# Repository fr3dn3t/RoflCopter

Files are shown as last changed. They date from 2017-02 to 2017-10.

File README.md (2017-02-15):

# RoflCopter
My RoflCopter makes swush swush swush - just kidding. The RoflCopter a monocopter, monospinner, gyropter, drone whatever you want to call it. 

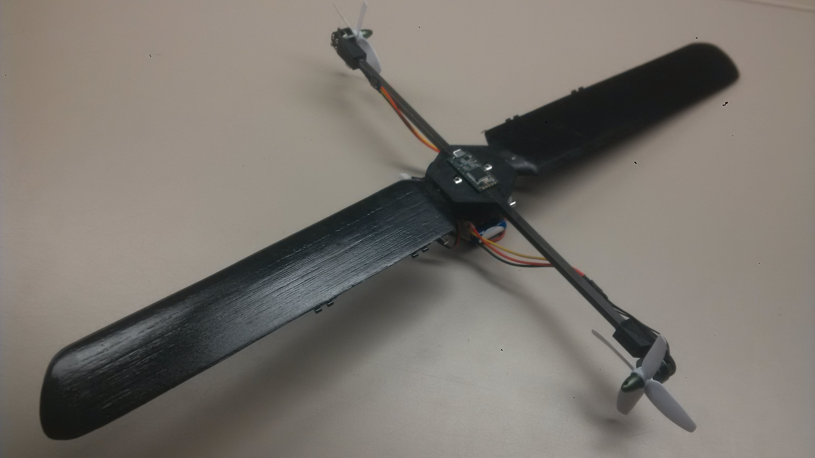
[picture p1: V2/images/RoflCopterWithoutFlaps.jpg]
roflCopter


I'm working on this project since October 2015 and until now, there have been two versions. The first Version was built to test various parameters and hardware approaches to make it fly - Version 1 was completed in May 2016, but never flew.
Applying the lessons learned from the first version I started to build a secont one. This one was completly designed via CAD and the rotor blades were simulated in XFLR5. A full documentation can be found in V2/docs/ (german only), the first successful flight was on 14th February 2017 [Video](https://github.com/fr3dn3t/RoflCopter/blob/master/V2/videos/RoflCopter%20-%20FirstFlight14022017.mp4)

more to come

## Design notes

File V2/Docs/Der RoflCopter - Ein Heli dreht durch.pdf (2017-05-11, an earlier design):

# Der roflCopter - Ein Heli dreht durch

### Jugendforscht Technik 2017

### Frederik Dunschen

### 24. Februar 2017

Zusammenfassung

Was bedeutet es, ein eigenes Konzept fur ein Flugger ¨ | ät zu entwerfen, zu konstruieren und
letztendlich die Algorithmen fur die Flugsteuerung zu implementieren? Dies untersuche ¨ ich in diesem Projekt anhand des RoflCopters. Der RoflCopter ist ein von mir entworfenes Kleinstfluggerät, das auf dem Prinzip eines Monocopters basiert. Das bedeutet, dass der
Auftrieb uber zwei Rotorbl ¨ | ätter erfolgt, die am Gehäuse des Copters befestigt sind. Das
gesamte System wird von zwei Motoren an einem Motorausleger in Rotation versetzt
und der Auftrieb uber den Anstellwinkel der Rotorbl ¨ | ätter gesteuert. Um seine Lage bzw.
Position im Raum zu ändern, besitzt der RoflCopter zwei Steuerklappen an den beiden Rotorblattspitzen. Doch dieser Aufbau allein reicht nicht aus, um ein flugfähiges Gerät zu erhalten. Dazu ist auch ein Algorithmus nötig, der Steuerbefehle einließt, die nötigen Steueraktionen berechnet und schließlich, abgestimmt auf die Hardware, ausfuhrt. ¨

# Inhaltsverzeichnis

1 Einleitung | 3
2 Projektablauf | 5
3 Aufbau und Funktion | 6
4 Algorithmik | 11
5 Fazit | 16
6 Verzeichnisse | 17

# Kapitel 1

# Einleitung

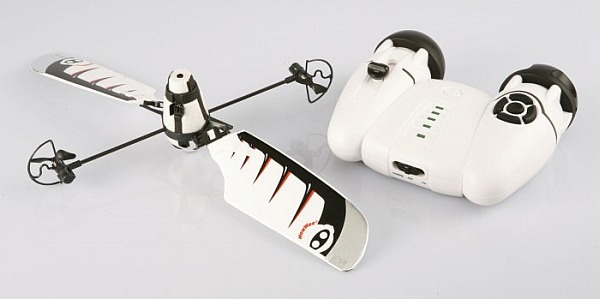
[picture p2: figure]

Abbildung 1.1: Bladestar [1]

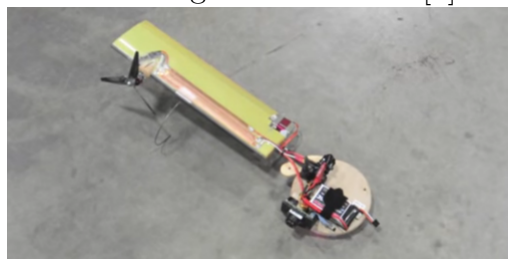
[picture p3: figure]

Abbildung 1.2: Samari UAV [2]

Der Traum vom Fliegen beflugelt seit jeher die ¨
kuhnsten Tr ¨ | äume der Menschheit. Waghalsige Kon-
struktionen folgten auf halsbrecherische Ideen und unzählige Absturze auf zahllose Flugversuche. Die ¨ ersten funktionierenden Fluggeräte, Flugzeuge wie Helikopter, ließen sich ausschließlich uber Mechani- ¨ ken steuern und fliegen, der Pilot bewegte Klappen und Ruder allein durch Muskelkraft. Undenkbar fur ¨ heutige Fluggeräte - Autopiloten und Flugassistenzsysteme nehmen Piloten viel Arbeit ab, Sensoren uberwachen jede kleinste Bewegung und Motoren ¨ fahren Klappen und Ruder aus und ein. Microcontroller und Computer haben jedoch nicht nur in großen Verkehrsmaschinen und Helikoptern Einzug gehalten. Sie ermöglichten Kleinstfluggeräte mit Konzepten, die mit einfacher Mechanik nicht realisierbar wären. Multicopter dienen hierfur als ¨
besonderes Beispiel: Die kleinen Fluggeräte sind
simpel Aufgebaut, flögen von sich aus jedoch nicht
stabil in der Luft. Erst die Flug- und Lageregelung durch einen kleinen Computer, einen
Microcontroller, erlaubt auch ungeubten Piloten das einfache Fliegen dieser Ger ¨ | äte. Der
Pilot steuert nicht mehr direkt, er gibt lediglich seinen Steuerwunsch an den Microcontroller weiter. Dieser kann die Daten, die fur die Steuerung relevant sind, wesentlich schneller ¨ und genauer messen, auswerten und interpretieren, um so das Fluggerät in Zusammenspiel mit der Mechanik letztendlich zu steuern.
Uber die letzten Jahre sind die Leistungsdaten von Microcontrollern erheblich gestiegen ¨
und die Preise gefallen. Das lässt nicht nur die Anzahl der verfugbaren, g ¨ | unstigen Kleinst- ¨
fluggeräte steigen, sondern ermöglicht es auch, innerhalb eines uberschaubaren Preisrah- ¨
mens, selbst ein Konzept fur ein Kleinstflugger ¨ | ät zu entwickeln und umzusetzen. Genau
dies habe ich mit dem roflCopter getan.
Der roflCopter ist zuerst einmal ein Rotationsflugler (daher der Name), er erzeugt den ¨ benötigten Auftrieb also durch einen rotierenden Flugel bzw. Rotor. Des weiteren ist er ¨ ein Fluggerät, dass von seiner Bauform her eine Art Monocopter ist. Ein Monocopter zeichnet sich dadurch aus, dass er nur ein Rotorblatt und keinen Drehmomentausgleich, wie beispielsweise den Heckrotor eines Helikopters hat. Das bedeutet, dass sich nicht nur der Rotor, sondern das gesamte Fluggerät in der Luft dreht. So ist es naturlich schwierig, ¨

KAPITEL 1. EINLEITUNG

in der Luft sowohl eine ruhige Fluglage, als auch eine Steuerung uber alle Achsen zu er- ¨ halten.
Der roflCopter basiert im Prinzip auf den Konzepten des “WowWee Bladestar” (Abb.: 1.1) und des “Lockheed Martin Samari UAV” (Abb.: 1.2). Diese Konzepte habe ich zusam-
mengefuhrt, da sie sich gegenseitig in ihren Vor- und Nachteilen erg ¨ | änzen. Der “WowWee
Bladestar” soll sich zwar steuern lassen, der technische Aufbau des Produktes lässt dies allerdings nicht zu: die Rotorblätter sind auf einen Winkel fest angestellt und nur die Motoren lassen sich in ihrer Umdrehungsgeschwindigkeit steuern. So lässt sich die Lage des
Copters naturlich nicht ver ¨ | ändern, das Fluggerät kann seine Position im Raum lediglich
auf der Z-Achse verändern, also steigen oder sinken.
Der “Lockheed Martin Samari UAV” hat, anders als der Bladestar, eine aktive Lageregelung. Hier ist auch der technische Aufbau ein anderer, es handelt sich um einen klassischen Monocopter bzw. Gyropter - die Entwickler haben sich von einem Ahornsamen inspirieren lassen. Doch durch den asymetrischen Aufbau und die daraus entstandene Unwucht fliegt der Copter nicht ruhig.
Ich versuche nun die Vorteile beider Konzepte zu verbinden: Den symetrischen Aufbau des “WowWee Bladestar” und die aktive Steuerung des “Lockheed Martin Samari UAV”. Mit diesem Projekt möchte ich untersuchen, wie aufwändig es ist und was es bedeutet, ein selbst konzipiertes Kleinstfluggerät zu entwickeln, das nur uber eine eigene, neuartige ¨ Flugsteuerung gesteuert werden kann. An Monocoptern als elektrisch betriebene Kleinstfluggeräte wird vergleichsweise wenig geforscht, es gibt nur vereinzelte Forschungsarbeiten von Universitäten wie der ETH Zurich [3], dem MIT [4], sowie der University of Maryland ¨
[5] und Firmen wie Lockheed Martin [6]. Auch dieser Umstand hat mich besonders an dem Bau eines solchen Fluggerätes gereizt, da ich nahezu alles selbst entwickeln muss. Eine weitere Herausforderung ist naturlich, die Hardware und die Software so zu konzipieren ¨ und aufeinander abzustimmen, dass sie möglichst schnell und präzise Steuerbefehle und Sensoren einlesen, die nötigen Berechnungen vornehmen und die jeweiligen Steueraktionen in entsprechende Flugbewegungen uberf ¨ uhren kann. ¨

# Kapitel 2

# Projektablauf

Die Idee fur den roflCopter hatte ich bereits im September 2015. Ich habe die ersten ¨
Entwurfe gemacht und angefangen, Bauteile f ¨ | ur einen Prototypen zu fertigen und zu be- ¨
stellen.
Den ersten Satz Rotorblätter habe ich im Oktober 2015 gefertigt. Diese habe ich an ein Grundgerust, bestehend aus dem Motorausleger mit entsprechenden Motoren, Motorreg- ¨ lern und Servos, angebracht. Gegen Ende Oktober habe ich mit der Steuerelektronik und der Software angefangen. Zu diesem Zeitpunkt hatte ich noch keine Steuerklappen vorgesehen, sondern wollte die Servos an den Rotorblättern zur Steuerung benutzen. Es hat sich jedoch herausgestellt, dass diese in ihrer Reaktion zu träge sind. Deshalb habe ich nach einer anderen Lösung gesucht und bin so auf die linearen Magnetaktuatoren gekommen. Im November und Dezember 2015 habe ich mich mit der Lagesensorik beschäftigt. Ich habe zunächst auch einen Kompasssensor verbaut, musste jedoch feststellen, dass dieser
Sensor zu langsam fur eine genaue Messung w ¨ | ährend der Rotation war.
Im Januar 2016 habe ich die Steuerklappen an den Rotorblättern installiert und die Elektronik zur Ansteuerung der Magneten entworfen. Sowohl die Schaltung, als auch die Klappenmechanik hat sich bewährt und ist bis heute die selbe geblieben. Im März habe ich die grundlegenden mathematischen Algorithmen zu Stabilisierung und Lageänderung entworfen und mit dem Bau des Infrarotmoduls begonnen.
Im April konnte ich anfangen, alle einzelnen Module fur die erste Version des Copters ¨ zu testen und zu verbessern. Ende April habe ich mit den Tests des gesamten Systems angefangen und konnte dabei Umdrehungsgeschwindigkeiten und Lagemessungen prufen. ¨ Die erste Version des roflCopters war fertig und ich konnte im Mai meine Facharbeit uber den Copter abgeben. Letztendlich hat sich jedoch herausgestellt, dass erste Ver- ¨
sion zwar genugend Auftrieb f ¨ | ur einen Flug erzeugt, jedoch trotzdem flugunf ¨ | ähig ist:
Die Aufhängung der Rotorblätter war zu instabil, die elektronischen Komponenten nicht geordnet bzw. symmetrisch aufgebaut und der gesamte technische Aufbau nicht aerodynamisch durchdacht.
Ab September habe ich eine zweite Version des Copters auf der Grundlage der Erkenntnisse der ersten Version konzipiert. Diesmal begann ich nicht mit dem Bau, sondern fing an, das System als 3D Modell zu entwerfen und wichtige Teile, wie die Rotorblätter, am
Computer zu simulieren. Daruber hinaus habe ich gepr ¨ | uft, welche Komponenten in der ¨
ersten Version wie gewunscht funktionierten und welche ich ersetzen musste. Die wich- ¨ tigste Anderung war die Konzeption eines um einen Lagerblock zentralisierten Aufbaus. ¨ Die Elektronik ist in der zweiten Version auch nicht mehr lose verkabelt, sondern auf einer Platine unter dem Lagerblock angebracht. Mit dem Bau der zweiten Version beschäftige ich mich seit Oktober 2016, der erste erfolgreiche Flug war am 14.02.2017 [18].

# Kapitel 3

# Aufbau und Funktion

## 3.1 Technischer Aufbau

Der roflCopter (Abb. 3.1) ist im Wesentlichen aus drei flugrelevanten Elementen aufgebaut: Dem antreibenden Element, dem auftreibenden Element und dem lageverändernden Element. Das Zusammenspiel dieser drei Elemente ermöglicht den Flug des Copters.
Zwei burstenlose Elektromotoren der Baugr ¨ | öße 1304 mit zwei 3030 4-Blatt Propel-
lern stellen das antreibende Element. Die Motoren sind in die jeweils entgegengesetzte Richtung zeigend an den Enden eines 32cm langen
Motorauslegers, einem 6mm Carbon-Vierkantsab,
befestigt. Dazu habe ich die entsprechenden Motorhalterungen selbst designt und 3D gedruckt. Da die Motoren jeweils in die entgegengesetzte Richtung zueinander angebracht sind, können sie den Copter in die benötigte Rotation versetzen, ihn also antreiben. Die Drehfrequenz bleibt während des Fluges näherungsweise gleich. Um möglichst viel


Abbildung 3.1: Gesammtansicht des rofl-Copters [11]
Zugkraft pro Motor bei kleinstmöglicher Größe zu ermöglichen, habe ich nach versuchen mit verschiedenen Propellern, Propeller mit vier Blättern gewählt.
Welcher Teil des roflCopters das auftreibende Element ist, zeigt sich schon an seinem
Namen. Er ist ein Rotationsflugler, das auftreibende Element ist der rotierende Fl ¨ | ugel bzw. ¨
Rotor. Dieser hat die Maße von 250mm ∗ 55mm
und ist im Winkel von 90◦
zum Motorausleger angebracht. Auf die aerodynamischen Eigenschaften werde ich später noch eingehen. Beide Rotorblätter sind jedoch nicht starr verbaut, sondern lassen sich uber Modellbauservos kippen und in ihrem An- ¨ stellwinkel verändern. Hier zeigt sich auch, das die Rotorblätter nicht nur aufgrund ihres Flugelprofils ¨ das auftreibende Element des Copters sind, sondern auch, weil die eigentliche Auftriebssteuerung
nicht uber ein Ver ¨ | ändern der Drehfrequenz geregelt
wird, sondern bei konstanter Drehfrequenz uber ein ¨

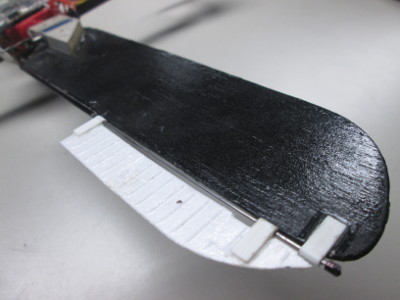
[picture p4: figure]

Abbildung 3.2: Steuerklappe am Rotorblatt; Prototyp V.1 [11]

Verändern des Anstellwinkels beider Rotorblätter. Dieses Prinzip nennt sich kollektiver Pitch und wird in jedem Helikopter angewendet, da das Steuern der Steig- und Sinkrate
uber das Ver ¨ | ändern der Drehfrequenz des Hauptrotors, des permanenten Beschleunigens
und Bremsens des Rotors, einerseits zu träge und andererseits zu energieaufwändig wäre.

KAPITEL 3. AUFBAU UND FUNKTION | 3.1. TECHNISCHER AUFBAU

Mit den beiden vorgestellten Elementen ließe sich der Copter zwar fliegen, eine Lagebzw. Positionsänderung im Raum wäre jedoch nicht möglich. Dazu wurde dem Copter die ¨ Möglichkeit fehlen, kontrolliert zu kippen und so in eine gewunschte Richtung zu fliegen. ¨ An dieser Stelle kommen die Klappen an den Rotorblattspitzen zum Einsatz (Abb. 3.2 und Abb. 4.5 - 4.8) - sie stellen das lageverändernde Element. Die Steuerklappen können uber lineare Magnetaktuatoren (Abb. 3.6), kleine elektromagnetisch steuerbare Kolben, ¨ sehr schnell an- und abgestellt werden. Die lineare Bewegung wird uber ein Ruderhorn und ¨ das daran angeschlossene Gestänge in eine Drehbewegung umgelenkt und auf die Steuerklappe ubertragen. So kann einem Rotorblatt bzw. einer Seite des roflCopters an einer ¨ bestimmten Stelle während der Umdrehung kurzzeitig mehr Auftrieb verschafft werden, als der anderen Seite. Dies bewirkt eine leichte Kippbewegung in die gewunschte Richtung ¨ (genauer erläutert in Abschnitt 4.3). Auch dieses Prinzip ist im Helikopter umgesetzt; es wird zyklischer Pitch genannt.

Eine weitere wichtige Voraussetzung fur den Flug des roflCopters ist ein Design, ¨ dass möglichst symmetrisch aufgebaut ist, um keine Unwucht zu erzeugen. Dazu gehört, möglichst alle schweren Bauteile, wie Elektronik,
Servos oder den Akku zu zentralisieren und in der
Mitte des Fluggerätes möglichst kompakt anzuordnen. Eine kompakte Anordnung in der Mitte ist auch insofern wunschenswert, als dass sie aerody- ¨ namisch gesehen die bremsende Angriffsfläche fur ¨ die bei der Rotation entstehenden Luftströme minimiert. Zu diesem Zweck habe ich einen sechseckigen Lagerblock designt (Abb. 3.3), der im Zentrum des roflCopters sitzt. An diesem Lagerblock sind die

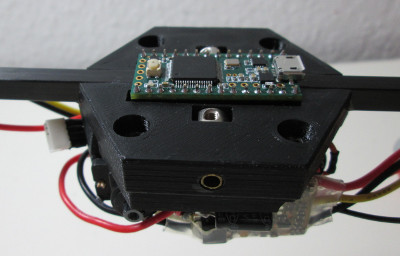
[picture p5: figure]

Abbildung 3.3: Lagerblock mit Teensy 3.2 [11]
beiden Rotorblätter und der Motorausleger befestigt; hier wird das antreibende Element mit dem auftreibenden verbunden. Das bedeutet jedoch auch, dass in diesem Lagerblock alle Belastungen, die auf diese Bauteile wirken, zusammenlaufen und absorbiert werden
mussen. Gerade die Rotorbl ¨ | ätter mussen hier so befestigt sein, dass alle entstehenden ¨
Kräfte zwar gehalten werden können, sich die Rotorblätter aber dennoch kippen lassen. Ermöglicht wird dies durch die Messing-Gleitlager im Lagerblock und die Stellringe, mit denen die Rotorblätter fixiert werden (siehe Abb. 3.3). Da daruber hinaus alle Bauteile ¨ des Copters am Lagerblock befestigt sind, trägt er zwar die gesamte mechanische Belastung des Copters, muss aber trotzdem so leicht wie möglich sein. Deshalb habe ich auch dieses Bauteil 3D gedruckt.
Unter dem Lagerblock ist die Hauptplatine mit der Mess-, Steuer- und Funkelektronik angebracht. Die Schaltung auf der Platine und das Platinenlayout habe ich mithilfe der Software ”KiCad” entworfen und die Platine in einem Atzbad hergestellt. Da auf ¨ dieser Platine auch der Lagesensor sitzt, ist diese jedoch nicht direkt am Lagerblock angeschraubt. Sie ist vielmehr zwischen zwei Gummiringen eingeklemmt und damit schwingungsgedämpft aufgehangen. Außerdem ist der Spalt, der zwangsweise zwischen Platine und Lagerblock entsteht, durch eine Abschirmung vor den Luftströmen geschutzt, die ¨ beim Rotieren entstehen. Beides dient dazu, um den Lagesensor vor den Vibrationen zu
schutzen, die w ¨ | ährend des Fluges entstehen und auf den Lagerblock ubertragen werden. ¨
Um den Aufbau noch kompakter halten zu können, habe ich den Microcontroller nicht direkt auf der Platine angebracht, dieser befindet sich oben auf dem Lagerblock (Abb.
3.3) und ist uber Pinheader mit der Platine und den anderen Modulen verbunden. ¨ Unter der Platine befinden sich die zwei Modellbauservos, die den Anstellwinkel der Rotorblätter verändern, sowie die Motortreiber fur die Motoren und der Akku. ¨

3.2. FLUGRELEVANTE FUNKTIONEN KAPITEL 3. AUFBAU UND FUNKTION

## 3.2 Flugrelevante Funktionen

Fur den Flug des roflCopters spielen die Funktionen, die Eigenschaften und die Ausle- ¨ gung der Komponenten eine wichtige Rolle. Alles muss so leicht wie möglich, so stabil wie nötig und so schnell wie gewunscht funktio- ¨
nieren, um im Zusammenspiel ein flugfähiges
Gerät zu bilden. Aus diesem Grund ist es unumgänglich, Modell und Bauteile vor der Konstruktion am Computer als 3D Modell anzufertigen und uber Simulationen zu testen. ¨ Zunächst werde ich auf die aerodynamischen Eigenschaften der Rotorblätter eingehen und darauf auf die weitere Mechanik zu sprechen kommen. Die Rotorblätter habe ich mit Hilfe des Programms ”XFLR5” in ihrem Profil designt, simuliert und letztendlich als 3D Mo-

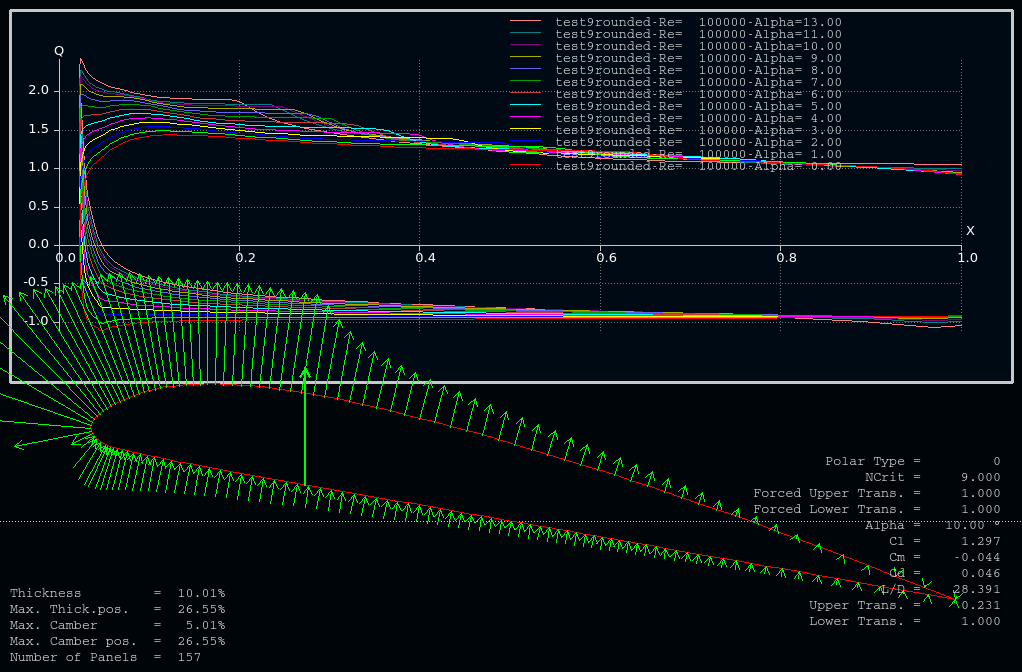
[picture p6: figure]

Abbildung 3.4: Auftriebsverteilung am verwendeten Rotorprofil [12]

dell angefertigt. Uber die Simulation konnte ich zum Beispiel feststellen, wie groß der ¨ Auftrieb des Rotors bei einem bestimmten Anstellwinkel ist und dass bei einem Anstellwinkel von 10◦ der Quotient zwischen Auftrieb und Luftwiederstand maximal ist; der Rotor demzufolge bei diesem Anstellwinkel am effizientesten arbeitet. Die Simulationsergebnisse des letztendlich entstandenen Rotorprofils sind in Abbildung 3.4 dargestellt. Ein weiterer wichtiger Anspruch an das Profildesign war, dass es sich mit einer CNC Fräse aus Balsaholz fräsen lässt.
Wie bereits im vorherigen Abschnitt ”Technischer Aufbau” beschrieben, können die Rotorblätter mithilfe von Modellbauservos in ihrem Anstellwinkel verändert werden und bilden so eine Auftriebssteuerung nach dem
Prinzip des kollektiven Pitch. Der Aufbau der
Mechanik ist in Abbildung 3.5 dargestellt. Um
das Rotorblatt anzustellen, dreht sich der Servo (Abb. 3.5, rot eingefärbt) im Uhrzeigersinn. Uber den Servoarm wird diese Bewegung auf ¨ das Gestänge ubertragen, das den Servoarm ¨ und das Ruderhorn am Rotorblatt verbindet (Abb. 3.5, ebenfalls rot eingefärbt). Da das
Ruderhorn (Abb. 3.2, grun eingef ¨ | ärbt) paralell

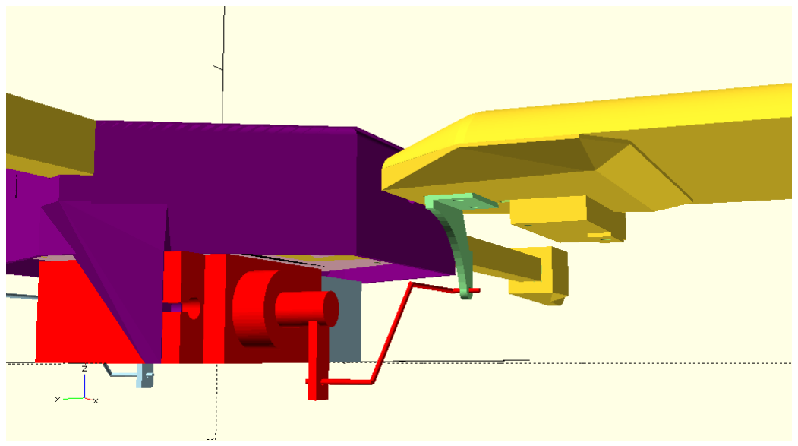
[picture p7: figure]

Abbildung 3.5: Servo und Gestänge zum Anstellen des Rotorblattes [13]
zur Lageraufhängung angebracht ist, dreht sich das Rotorblatt ebenfalls im Uhrzeigersinn und wird so um einen gewunschten Winkel angestellt. Beide Servos werden vom ¨
Microcontroller uber die selbe Signalleitung angesteuert und k ¨ | önnen so auf jeden belie-
bigen Winkel von 0◦ bis 180◦
eingestellt werden. Dabei haben sie einen Drehmoment
von ca. 20Ncm [7]. Allerdings sind die Servos recht langsam, fur eine Positions ¨ | änderung
von 60◦ benötigen sie ca. 110ms. Fur den roflCopter werden so große Stellwinkel zwar ¨
nie benötigt, jedoch dauert es aufgrund des Ubertragungsprotokolls f ¨ | ur Modellbauservos ¨
(Details dazu im nächsten Abschnitt) mindestens 20ms, bis ein Signal eingelesen wurde. Erst darauf beginnt der Servo mit der Bewegung. In dieser Zeit hat sich der roflCopter, bei einer angenommenen Drehfrequenz von ca. 13Hz, also ca. 800 U/min., schon

1sec=1000ms

13Hz=13U/1000ms = 76, 92ms = Dauer einer Umdrehung → 76,92ms
360◦ | = 0, 214ms = Dauer
einer Drehung von 1◦ → | 20ms
0,214ms/1
- = 93, 46◦ weitergedreht. Daraus folgt, dass die Servos

viel zu träge sind, um kurzzeitig ein Rotorblatt anders anzustellen um eine Lageänderung zu erzeugen und so den Copter zu steuern.

KAPITEL 3. AUFBAU UND FUNKTION 3.3. HARDWARE UND KOMPONENTEN

Zu diesem Zweck verwende ich lineare Magnetaktuatoren, auch solenoid actuator oder einfach solenoid genannt, die eine Steuerklappe an der Rotorblattspitze anstellen. Im Prinzip handelt es sich dabei um einen Elektromagneten, der einen Kolben anzieht und so
eine lineare Bewegung ausfuhrt. Der Elektro- ¨
magnet kann allerdings sehr schnell geschaltet werden, ich habe in praktischen Tests herausgefunden, dass die Steuerklappe innerhalb von ca. 2ms - 3ms angestellt werden kann, wenn der solenoid auf die Akkuspannung von ca. 8V geschaltet wird. So kann das Funktionsprinzip des sogenannten zyklischen Pitch angewendet werden. Das bedeutet fur den roflCopter, dass ¨ durch Anstellen einer Steuerklappe innerhalb eines Teiles einer Umdrehung ein Rotorblatt

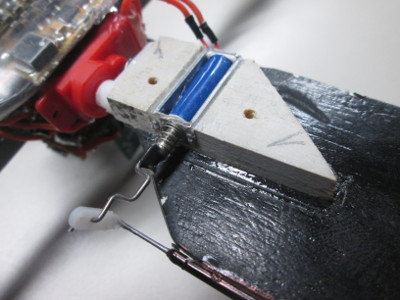
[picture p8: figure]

Abbildung 3.6: Solenoids und Gestänge fur die ¨ Steuerklappen; Prototyp V.1 [11]

mehr Auftrieb bekommt, als das andere. Durch diese Auftriebsdifferenz kippt der Copter
leicht in die gewunschte Richtung und kann gesteuert werden. Die Solenoids sind ¨ | uber ein ¨
Gestänge mit den Steuerklappen verbunden; der Aufbau ist in Abbildung 3.6 dargestellt. Eine weitere flugrelevante Funktion stellt auch die Anordnung der Komponenten unter der Höhe der Rotorblattachse dar. Dadurch, dass Servos, Motorregler und Akku als schwerste Komponenten unter dem Lagerblock sitzen und möglichst kompakt angeordnet sind, sitzt der Schwerpunkt des Copters sowohl in der Mitte des Fluggerätes, jedoch auch unter der Höhe der Rotorachse. So kann der Copter unwuchtsfrei drehen und wird durch die tieflastige Anordnung der Komponenten automatisch in eine waagerechte Fluglage gezogen. Diese passive Stabilisierung allein reicht fur einen stabilen waagerechten Flug nicht aus, ¨
da dafur das Tr ¨ | ägheitsmoment verglichen mit der Bewegung in den drei Raumachsen zu
groß ist. Die aktive Lagerregelung wird daher durch die Steuerklappen ubernommen, die ¨ Stabilisierung in der waagerechten Fluglage jedoch erheblich unterstutzt. ¨

## 3.3 Hardware und Komponenten

In diesem Abschnitt möchte ich darauf eingehen, welche elektrotechnischen Komponen-
ten fur die Steuerung des roflCopters verbaut wurden. Das ”Herzst ¨ | uck”des Copters ist ¨
der Microcontroller. Dieser kleine Computer nimmt alle Steuerbefehle des Piloten entgegen, wertet die Sensoren aus, berechnet die nötigen Steueraktionen und fuhrt diese aus. ¨ Als Chip kommt ein ARM Cortex M4 Microcontroller auf einem Teensy 3.2 Board zum Einsatz. Dieser Prozessor hat nicht nur die entsprechend benötigten Leistungsdaten (u.a. 144MHz Taktgeschwindigkeit), sondern auch mehrere Hardwaretimer. Diese Hardwaretimer ermöglichen, dass der Microcontroller die Steuerbefehle des Piloten entgegen nehmen kann, während gleichzeitig und zum richtigen Zeitpunkt die Steuerklappen mit Signalen versorgt werden können. Anders gesagt ermöglichen die Hardwaretimer eine Form der
Parallelisierung fur die zu bew ¨ | ältigenden Aufgaben, ohne das die Software durchs Warten
auf Ereignisse gelähmt und das Ausfuhren anderer Aktionen behindert wird. Der ARM ¨
Cortex M4 Prozessor auf dem Teensy 3.2 kombiniert alle gewunschten Eigenschaften f ¨ | ur ¨
den Copter: Er ist klein, leicht und hat außreichend Rechenleistung.
Der Grundstein, auf dem die Lageregelung basiert, ist der Lagesensor. Hier kommt ein MPU9250 von Ivensense zum Einsatz. Dieser Sensor kombiniert einen 3-Drehratensensor, einen 3-Achs Beschleunigungssensor und einen 3-Achs Kompass. Mithilfe dieser Sensoren kann der roflCopter seine Lage im Raum bestimmen und entsprechende Steueraktionen

3.4. KEIN FLUG OHNE SOFTWARE | KAPITEL 3. AUFBAU UND FUNKTION
ausfuhren, um einen stabilen Flug zu gew ¨ | ährleisten.
Um die Steuerbefehle des Piloten entgennehmen zu können, benötigt der roflCopter einen
passenden Empfänger fur die Fernbedienung. Als Fernsteuersystem habe ich mich f ¨ | | ur ¨
das Taranis System von FrSky entschieden, weil es einerseits das sehr schnelle Ubertra- ¨ gungsprotokoll ACCST nutzt, das Steuerbefehle mit einer Latenz von nur ca. 7ms ubertr ¨ ägt. Ein weiterer Vorteil ist die große Verbreitung und damit auch die Verfugbarkeit sehr klei- ¨ ner Empfängerplainen , da diese in sehr vielen Wettkampfquadrocoptern verbaut werden. Da es sich bei den Motoren des roflCopters um burstenlose Motoren, sogenannte BLDCs ¨ handelt, können diese nicht einfach uber das Anlegen einer Gleichspannung in Drehung ¨
versetzt werden. Burstenlose Motoren, im Fall des roflCopters b ¨ | urstenlose Außenl ¨ | äufer
(Abb. 3.1), haben drei voneinander getrennte Motorphasen, die jeweils alternierend zueinander auf dem Stator angebracht sind. Diese werden entsprechend der Ausrichtung des Rotors nacheinander angesteuert. So ergibt sich ein annähernd kreisförmiges Drehfeld zwischen Rotor und Stator, das den Rotor in Drehung versetzt. Die Motorregler, die ich im roflCopter verbaut habe, stammen ebenfalls auf dem Modellbaubereich und ubernehmen ¨ genau diese Aufgabe. Angesteuert werden sie genau so, wie die Modellbauservos, die den Anstellwinkel der Rotorblätter steuern. Mehr dazu in Abschnitt 4.1
Um seine Ausrichtung im Raum relativ zum Piloten bestimmen zu können, ist im rofl-Copter ein Infrarot-Empfänger Typ TSOP38238 verbaut. Dieser hat ebenfalls nur eine Signalleitung, die entweder an oder aus ist, je nachdem, ob ein Signal empfangen wurde oder nicht. Um nicht von anderen Infrarot aussendenden Lichtquellen, besonders der Sonne, gestört zu werden, nimmt der Sensor nur Signale an, die auf einer Wellenlänge von 940nm mit 38kHz gepulst werden. Wie genau der Microcontroler das Signal des IR-Empfängers auswertet ist in Abschnitt 4.2 beschrieben.
Neben der Kommunikation mit dem Piloten in Form des Einlesens der Steuerbefehle muss der Copter ebenfalls mit einem Computer kommunizieren können, um beispielsweise Debug Informationen bzw. Telemetriedaten, wie den Ladestand des Akkus, zu
ubermitteln. Dies gew ¨ | ährleistet den sicheren Betrieb und vermeidet Unfälle sowie un-
kontrollierte Absturze. Zu diesem Zweck habe ich ein kleines Bluetooth Modul eingebaut. ¨ Dieses sendet einfache Zeichenketten, die uber eine serielle RX/TX Schnittstelle eingege- ¨ ben werden.

## 3.4 Kein Flug ohne Software

Auf Grund der hohen Rotationsgeschwindigkeiten und der dadurch erforderlichen, kurzen Reaktionszeiten ist eine lageregulierende Software fur einen stabilen Flug unabdingbar. ¨ Dabei wird diese Flugweise vor allem durch zwei Faktoren erschwert. Einerseits fliegt der Copter nicht eigenstabil, das bedeutet, dass er nicht ohne eine aktive Steuerung geradeaus fliegt. Man kann das gut mit dem Balancieren eines Stiftes auf der Hand vergleichen. Es mussen andauernd kleine Korrekturen der Lage vorgenommen werden, um den Co- ¨
pter nicht aus der gewunschten Flugbahn ausbrechen zu lassen. Andererseits m ¨ | ussen alle ¨
Berechnungen und Steueraktionen in einer Umdrehungszeit von 50ms - 100ms schnell
erfolgen. Der menschliche Pilot ist fur die notwendigen Korrekturen zu reaktionstr ¨ | | äge,
wobei diese Korrekturen teilweise auch noch gleichzeitig erfolgen mussen. Somit ist die ¨ Verwendung einer geeigneten Software, die die Steuerbefehle an die Regelstrecke weitergibt, die letztendlich die Steueraktionen bestimmt, notwendig. Zusätzlich zur Latenzzeit kommt der Umstand, dass der Pilot sich nicht im Fluggerät befindet und somit nötige Lageausrichtungen nicht erkennen kann. Auch dies muss in der Boardsoftware automatisiert hinterlegt sein.

# Kapitel 4

# Algorithmik

Im folgenden Teil der Arbeit werde ich nur auf die verwendeten Prinzipien der Software und Algorithmik eingehen. Programmcodes werde ich nicht einbinden, da sich diese noch laufend ändern;
sie werden aber alle in meinen github repository veröffentlicht: https://github.com/fr3dn3t/RoflCopter

## 4.1 Ansteuerung von Servos und ESCs

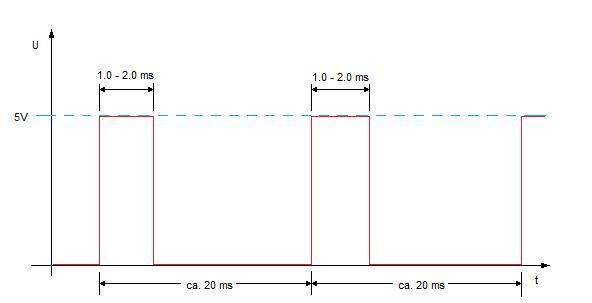
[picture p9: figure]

Abbildung 4.1: Servo Impulsdiagramm [8]

Wie schon erwähnt, stammen die Servos und Motorregler aus dem Modellbaubereich. Da es dort ublich ist, das diese Komponenten direkt an den ¨ Modellbauempfänger oder einen Flugregler angeschlossen werden und sofort funktionieren (Plug and Play), beschränkt sich die einseitige Kommunikation zwischen Bauteilen einerseits auf das Wesentliche (die Ubertragung der Steuerinformationen von ¨ Empfänger zum Bauteil) andererseits wird ein sehr einfaches Protokoll bzw. eine sehr einfache Modu-
lation fur die Daten ¨ | ubertragung genutzt, die so- ¨
genannte Pulsweitenmodulation, kurz PWM. Diese
benötigt nur eine Signalleitung, die zwei Zustände annehmen kann: ”An” oder ”Aus”. ”An” bedeutet in diesem Fall, dass die Spannung auf der Signalleitung gleich der Versorgungsspannung des Bauteils ist (in der Modellbautechnik ublicherweise 5V) und ”Aus”, ¨ dass die Signalleitung aus Masse geschaltet ist. Pulsweitenmodulation bedeutet nun, dass es innerhalb eines festgelegten Zeitraumes, einer Periode, einen Puls gibt, dessen Länge
variieren kann, um einen bestimmten Wert zu ubertragen. Im Modellbaubereich betr ¨ | ägt
die Länge des festgelegten Zeitraumes, die Periodendauer, 20ms. Innerhalb dieser 20ms gibt es nun einen Puls, dessen Länge zwischen 1ms und 2ms variieren kann (siehe Abb. 4.1), wobei 1ms das mögliche Minimum und 2ms das mögliche Maximum der Aussteuerung darstellt. Minimum bedeutet bei einem Servo 0◦ und bei einem Motorregler keine Motordrehung, Maximum bedeutet bei einem Servo 180◦ und bei einem Motorregler die maximal mögliche Geschwindigkeit des Motors. Der Microcontroller muss nun diese Protokoll anwenden um Servos und Motorregler anzusteuern. Normalerweise werden alle Servos und Motorregler mit einer eigenen Signalleitung angesteuert, im Falle des RoflCopters sind die Signalleitungen jedoch zusammengefasst. Dies ist möglich, da die Servos ausschließlich
den kollektiven Pitch uber das Verstellen des Anstellwinkels der Rotorbl ¨ | ätter steuern und
deshalb immer auf den selben Winkel eingestellt werden. Auch die Motoren sollen gleich schnell drehen, deshalb nutzen auch sie die selbe Signalleitung.

4.2. ROTATIONSBESTIMMUNG IM RAUM | KAPITEL 4. ALGORITHMIK

## 4.2 Rotationsbestimmung im Raum

Fur die Steuerung des ROFL-Copters ist es unerl ¨ | ässlich, dass seine Ausrichtung zum
Piloten bekannt ist. Gibt dieser den Steuerbefehl ”nach vorne fliegen”, so muss sich der Copter vom Piloten wegbewegen. Außerdem muss
die Umdrehungszeit und -geschwindigkeit bekannt
sein, um mit diesen Werten die aktuelle Lageabweichung und letztendlich die Ansteuerzeiten fur die ¨ Klappen berechnen zu können.

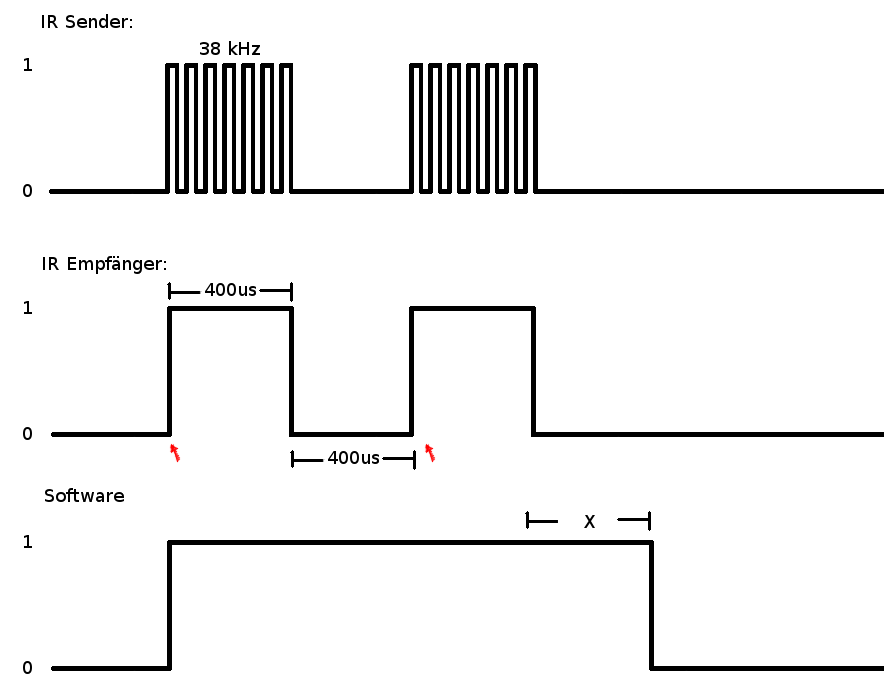
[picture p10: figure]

Ich habe diese Probleme mit einem Infrarotempfänger gelöst, der nach einem Infrarotsender sucht. Der andauernd sendende Sender, das infrarot Leuchtfeuer, ist unter der Fernsteuerung angebracht (Abb.
4.3). Ursprunglich hatte ich vor, das Licht ¨ | uber ei- ¨
ne Sammellinse zusätzlich zu bundeln, in der Pra- ¨ xis hat sich jedoch herausgestellt, das dies nicht

Abbildung 4.2: Infrarotsignal Impulsdiagramm [14]
praktikabel ist. Es funktioniert besser, wenn die LED möglichst weit streut, um eine zuverlässige Verbindung zum Copter herzustellen. Der IR Empfänger befindet sich im
Lagerblock des roflCopters. So ist sein Offnungswinkel ¨ | uber eine 0,6mm breite, ca. 1mm ¨
tiefe Blende nur in eine Richtung hin eingeschränkt.

Wie in Abschnitt 3.3 beschrieben ist nimmt der Empfänger generell nur Infrarotsignale an, die mit 38kHz gepulst wurden. Wenn er jetzt also ein solches Infrarotsignal empfängt, gibt der Empfänger an den Microcontroller eine logische 1 zuruck, ansonsten eine logi- ¨
sche 0.
Da der Empfänger, der fur Daten ¨ | ubertragung ¨ | uber ¨
IR konzipiert ist, keine anhaltenden Signale bzw. Zustände weitergeben kann, sendet der Sender nicht einfach den Dauerzustand 1, sondern wechselt alle 400us zwischen 0 und 1.
Die Software muss die eingehenden Signale nun so interpretieren, dass der andauernde Wechsel zwischen 0 und 1 innerhalb von 400us einer logischen 1 und das Anliegen einer 0 fur mindestens 800us ¨

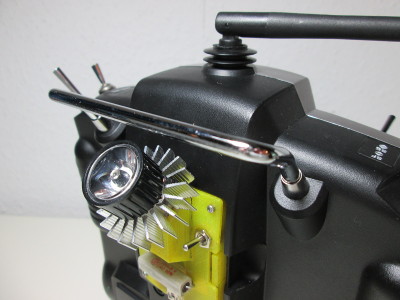
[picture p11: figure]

Abbildung 4.3: Infrarotsender mit Sammellinse an der Fernsteuerung [11]

einer logischen 0 entspricht (siehe Abb. 4.2). Zusätzlich kann eine Pufferzeit hinzugefugt ¨ werden (x in Abb. 4.2), die verhindert, dass zu schnell angenommen wird, dass sich der Copter bereits aus dem Infrarotstrahl des Senders herausgedreht hat und so bei einer erneuten Verbindung angenommen wurde, dass sich der Copter in der Zwischenzeit einmal ¨ gedreht hätte. Jedes Mal, wenn das Eingangssignal von 0 auf 1 wechselt (rote Pfeile in Abb. 4.2), wird ein Interrupt innerhalb des Microcontrollers aufgerufen, der die Regel-
schleife fur die Lageregelung anst ¨ | ößt. Dies passiert, da der Microcontroller nun feststellen
kann, dass der Copter mit dem IR Empfänger in Richtung des Piloten ausgerichtet ist und so seine Steuerbefehle passend interpretieren kann. Konkret bedeutet dies, dass wenn der Pilot den Befehl ”nach vorne fliegen” gibt, der Copter weiß, dass er bei seiner aktuellen Umdrehungsgeschwindigkeit noch x Millisekunden warten muss, bis er eine Steuerklappe
anstellt, um die gewunschte Lage ¨ | änderung vorzunehmen.
Neben der Bestimmung der Ausrichtung des Copter relativ zum Piloten kann uber den ¨ IR-Empfänger ebenfalls die aktuelle Umdrehungsgeschwindigkeit sehr genau gemessen werden. Dazu misst der Microcontroller einfach die Zeitdifferenz zwischen den Pulsen, die

KAPITEL 4. ALGORITHMIK 4.3. BERRECHNUNGEN ZUR LAGEANDERUNG ¨

vom IR Empfänger weitergegeben werden. Beträgt die Zeit zwischen den Pulsen beispiels-
weise 100ms kann errechnet werden, dass der roflCopter mit | 1min
100ms/U=0.1min/U = 600U/min
dreht.

## 4.3 Berrechnungen zur Lageänderung

### 4.3.1 Abgleich von IST und SOLL Werten

Durch das Einlesen des Beschleunigungs- und Drehratensensors und anschließendem fusionieren und filtern der jeweiligen Sensorwerte mithilfe des Kalman Filters [16] ist bekannt, wie der Copter im Raum liegt. Da jedoch nur an einer Stelle jeder Umdrehung bekannt
ist, wie der Copter ausgerichtet ist, nämlich wenn
der IR Empfänger eine Sichtverbindung zu dem IR Sender hat, kann auch nur an dieser Stelle die Lage des Copters mit dem Lagesensor eingelesen werden,
da sich das feste Koordinatensystem innerhalb des
Lagesensors während der Umdrehung des Copters

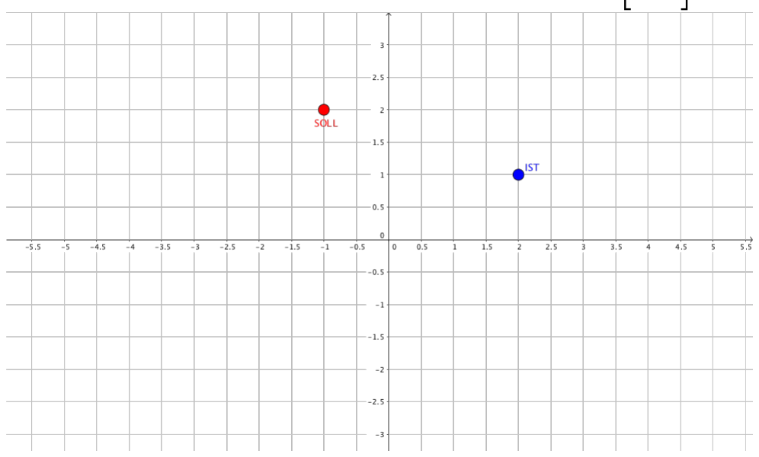
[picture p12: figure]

ebenfalls dreht. Wird an dieser Stelle gemessen und Abbildung 4.4: IST und SOLL Punkt [15] die Regelschleife angestoßen, gibt es einen aktuellen IST Wert. Der Pilot des roflCopters sendet uber die Fernsteuerung die Steuerbefehle. Sie definieren den SOLL Wert. Die Auf- ¨ gaben der Flugsteuerung ist nun, einen Weg von IST zu SOLL zu finden und den Copter dementsprechend zu steuern.
Im Fall des roflCopters beinhaltet sowohl der IST, als auch der SOLL Wert die Information uber den Kippwinkel auf der X als auch auf der Y Achse in Bezug auf den Piloten. Die ¨ Werte kann man als Punkte in ein Koordinatensystem eintragen. Einen IST-Punkt und einen SOLL-Punkt mit den dazugehörigen X|Y Koordinaten. Im Beispiel sind die Werte
IST = (2 | 1) und SOLL = (-1 | 2) (Abb.: 4.4).
Zur weiteren Veranschaulichung der Regelschleife zieht man die SOLL Werte von den IST Werten ab, man verschiebt die Punkte auf dem Koordinatensystem also so, dass der SOLL-Punkt im Ursprung liegt.

### 4.3.2 Vektoren als Grundlage der Steuerung

Die verschobenen Punkte sind in Abb. 4.5 dargestellt und die Grafik des roflCopters so ausgerichtet, dass der Pilot an einem beliebigen Punkt Pn(0|n) fur ¨ n < 0 steht, die
Offnung der Blende f ¨ | ur den IR-Empf ¨ | änger dement-
sprechend in eben diese Richtung zeigt. Wenn man
nun den SOLL-Punkt als einen Kreismittelpunkt
ansieht, dessen Kreis durch den IST-Punkt verläuft und man diesen Kreis “Rotorkreis” nennt, lässt sich die nun folgende Berechnung weiter veranschaulichen - der Rotorkreis ist der Bereich, in dem sich der Rotor des ROFL-Copters dreht (siehe Abb.: 4.5).
Zeichnet man nun einen Vektor vom IST-Punkt

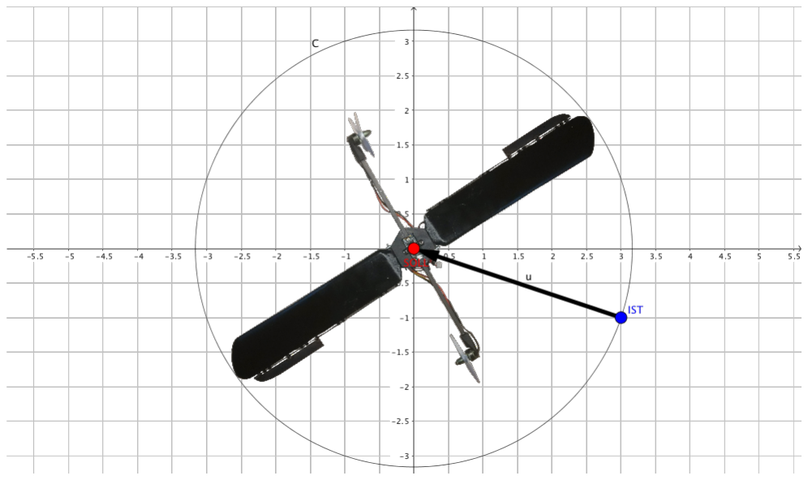
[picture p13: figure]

Abbildung 4.5: Rotorkreisfläche und Bewegungsvektor [15]

(blau) zum SOLL-Punkt (rot), erkennt man bereits einen Teil der Steuerung. Dies ist die Bewegung, die der Copter vollziehen soll, um entsprechend der Anweisung des Piloten zu fliegen bzw. zu kippen.
Allerdings ist der IST Punkt nicht die Stelle, an dem eine Steuerklappe angestellt wer-

4.3. BERRECHNUNGEN ZUR LAGEANDERUNG KAPITEL 4. ALGORITHMIK ¨

den muss, um dem dementsprechenden Rotorblatt kurzzeitig mehr Auftrieb zu verschaffen und in die gewunschte Richtung zu kippen. Auf- ¨
grund der Tatsache, dass der rCopter an sich mit
seinen verhältnismäßig weit außen liegenden Motoren und den Steuerklappen ein großes Gyroskop ist, unterliegen seine Bewegungen der Präzession [17] und sind jeweils 90◦
in Rotationsrichtung zu ihrer Ursprungskraft verschoben. Der eigentliche Steuerpunkt, an dem eine Klappe dem jeweiligen Rotorblatt kurzzeitig mehr Auftrieb verschaffen muss, sodass der Copter in Richtung des Bewegungsvek-

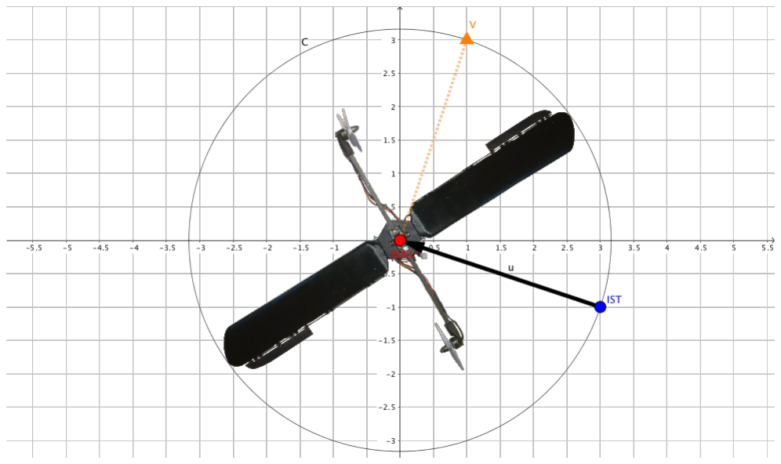
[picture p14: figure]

Abbildung 4.6: Steuerpunkt -90◦ zum
Bewegungsvektor[15]
tors −→u kippt, liegt im Rotorkreis des roflCopters dementsprechend 90◦ gegen den Uhrzei-

gersinn verschoben (siehe Punkt V (orange) in Abb. 4.6).
Nun ist der Punkt, an dem die Kraft zum kippen angelegt werden soll, bekannt, jedoch lässt sich diese Kraft durch die Steuerklappen nicht in nur einem Punkt konzentrieren. Außerdem muss noch eine Möglichkeit bestehen, die angebrachte Kraft zu verändern, um durch in der Stärke regelbare Kippimpulse genau zu steuern.

Beide Probleme lassen sich lösen, wenn festgelegt wird, dass eine Steuerklappe innerhalb eines um den Steuerpunkt V symmetrischen Bereiches angestellt wird. Der Bereich bzw. Winkel α, in dem die Klappe angestellt sein
soll, ist in Abb. 4.7 dargestellt. Dieser Winkel definiert, wie stark der Copter kippt (größerer Anstellwinkel → längere Anstellzeit der Klappe → mehr
Auftrieb fur das jeweilige Rotorblatt ¨ | → stärkerer
Kippimpuls).
Da der Copter also umso stärker kippen soll, je größer die Differenz zwischen dem IST und SOLL Wert ist, kann dieser Winkel einfach proportional zu dieser Differenz berechnet werden. Die Differenz

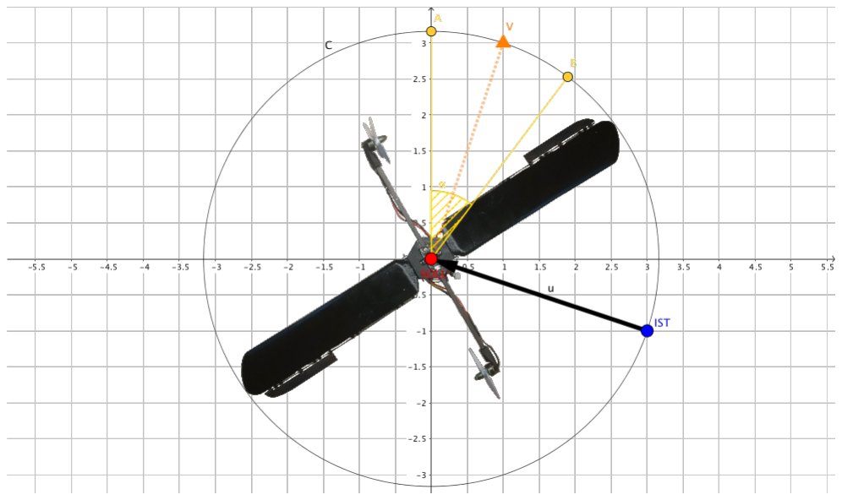
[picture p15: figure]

Abbildung 4.7: Klapenansteuerwinkel α [15]

und damit der Winkel bzw. Bereich α ist die Länge des Bewegungsvektors multipliziert mit x. x ist der Proportionalitätsfaktor (P-Wert) und damit eine einstellbare Größe der Regelung.

Da jetzt der Steuerbereich α der Klappe bekannt ist, muss nun ermittelt werden, welche der Steuerklappen zuerst angestellt werden soll. Die Ausrichtung des Copters ist zum Zeitpunkt der Berechnung bekannt (mit dem
IR-Empfänger zum Piloten), bei der nun folgenden Umdrehung im Uhrzeigersinn erreicht das in
den Grafiken unter der X-Achse liegende Rotorblatt die Quadranten I. und II., das oberhalb der X-Achse liegende Rotorblatt die Quadranten III. und IV. zuerst. Dementsprechend wird im vorliegenden Beispiel die Steuerklappe des unter der X-Achse liegenden Rotorblattes zuerst angestellt. Nun kann man auch beurteilen, ob es sich um einen

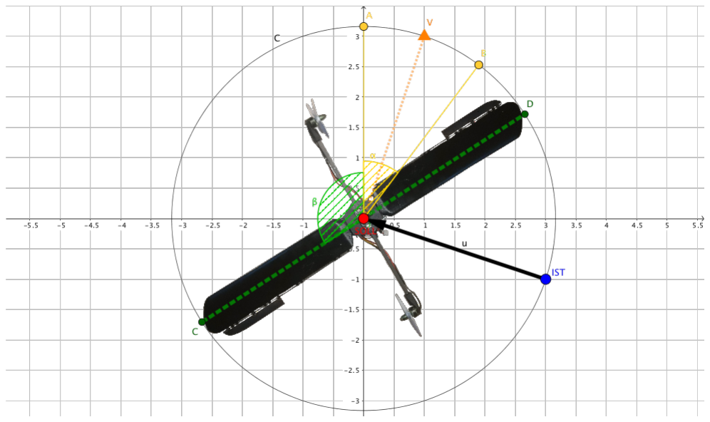
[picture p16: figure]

Abbildung 4.8: Winkel β bis zum Anstellen der Klappe [15]

stumpfen oder spitzen Winkel zwischen der aktuellen Ausrichtung und dem Ansteuerpunkt der Steuerklappe handelt und dementsprechend gerechnet werden. Im vorliegenden Beispiel liegt der Anstellpunkt der Klappe im I. Quadranten und damit in einem stumpfen Winkel zum Rotorblatt unter der X-Achse. Der Winkel zwischen der aktuellen Position und dem Anstellen der Klappe wird als Winkel β berechnet (siehe Abb. 4.8 (grun)). ¨

KAPITEL 4. ALGORITHMIK | | 4.4. START UND LANDESEQUENZ

### 4.3.3 Ermittlung von Zeiten zur Ansteuerung der Klappen

Mit den, wie in Abschnitt 4.3.2 gezeigt, verrechneten Winkeln α und β aus Abschnitt 4.3.2 und der mithilfe des IR Empfängers ermittelten Umdrehungsgeschwindigkeit kann man jetzt sehr simpel die Ansteuer- und Wartezeiten fur die Klappensteuerung berechnen. ¨
Die erste Zeit, die fur die Steuerung ben ¨ | | ötigt wird, ist die Zeit, die der Microcontroller
warten muss, bis er eine Steuerklappe anstellen soll. Diese Zeit setzt sich aus der letzten Umdrehungszeit geteilt durch den Anteil des Winkels β am Vollkreis, zusammen. Ein Beispiel: Die letzte Umdrehung hat 70ms = 70000us gedauert. Der errechnete Winkel β sei 105◦
. Dann beträgt die Zeit, die der Microcontroller warten muss, bis er die Steuerklappe anstellt 70000
(360/105) ≈ 20400us.
Genauso kann man mit dem Anstellwinkel α verfahren, um zu berechnen, wie lange die jeweilige Steuerklappe angestellt bleiben soll. An dieser Stelle werden die Hardwaretimer im Microcontroller eingestellt und so die Steuerklappen präzise und im richtigen Moment angesteuert, um den nötigen Kippeffekt zu erhalten. Nachdem die eine Steuerklappe wieder abgestellt wurde, werden die Timer so gesetzt, dass die Steuerklappe am anderen Rotor-
blatt die selbe Bewegung zur richtigen Zeit ausfuhrt und den Copter ein kleines St ¨ | uck ¨
weiter kippt. Nachdem dies ausgefuhrt wurde, wartet der Prozessor auf die Verbindung ¨ des IR Empfängers zum IR Sender und die Regelschleife beginnt von vorne.

## 4.4 Start und Landesequenz

Die Regelschleife läuft während des gesamten Fluges - außer in zwei Phasen: Start und Landung. An diesen Stellen kann die Lageregelung nicht funktionieren, da die Berechnung der Warte- und Ansteuerzeiten darauf basiert, dass die folgende Umdrehung ca. so lange dauern wird wie die vorherige. Da sich während des Starts und der Landung die Umdrehungsgeschwindigkeit jedoch andauernd ändert und jede folgende Umdrehung schneller bzw. langsamer ist, als die vorherige, funktioniert der Algorithmus zur Lageregelung hier
nicht. Aus diesem Grund mussen f ¨ | ur Start und Landung andere Abl ¨ | äufe implementiert
werden, als fur den normalen Flug. ¨
Ein Vorteil fur die Konzipierung dieser Abl ¨ | | äufe ist jedoch, dass sowohl die Start, als auch
die Landsequenz im Vergleich mit dem restlichen Flug nur sehr kurz ist - sie dauert nur einige Sekunden. An dieser Stelle ist die Tatsache wichtig, dass der roflCopter uber ei- ¨ ne passive und dauerhaft aktive Lagestabilisierung verfugt: Der tieflastige Aufbau der ¨ Komponenten wie Servos und Akku unter dem Lagerblock. Das bereits in Abschnitt 3.2 beschriebene Prinzip der passiven Stabilisierung, hilft bei Start und Landung erheblich, weil es eine aufwändige aktive Lageregelung an diesen Punkten ersetzt. Während des Starts und der Landung ist die aktive Lageregelung des roflCopters also abgeschaltet. Start: Der Copter wird vom Piloten mit der Hand angedreht und losgelassen. Die Bewegung des Andrehens und Loslassens wird vom Microcontroller als Spitze in den Werten der Z-Achse des Drehratensensors festgestellt. Daraufhin wird die Motorleistung und der Anstellwinkel der Rotorblätter maximiert, um den Copter schnellstmöglich in eine kon-
stante Rotation zu versetzen, die fur den Auftrieb n ¨ | ötig ist.
Landung: Zuerst steuert der Pilot den roflCopter auf eine Höhe von ca. 1m uber dem ¨ Boden, darauf aktiviert der die Landesequenz mit einem Schalter. Der Microcontroller deaktiviert die Regelschleife, bremst die Motoren und stellt die Rotorblätter auf einen flachen Winkel an. Das Aufsetzen auf dem Boden wird wieder als Spitze in den Werten des Lagesensors festgestellt. Daraufhin werden die Motoren abgestellt - Der roflCopter ist gelandet.

# Kapitel 5

# Fazit

Was lässt sich nun ruckblickend ¨ | uber dieses Projekt sagen? Einerseits gab es Abschnitte ¨
bzw. Aspekte des Projektes deren Umsetzung ich anfangs schwieriger eingeschätzt habe, als sie waren. Andererseits gab es auch Probleme, die deutlich komplizierter waren, als ich ursprunglich gedacht habe. ¨
Erstaunt hat mich, wie einfach der Algorithmus zur Berechnung der Steuerzeiten fur die ¨ Klappen letztendlich war. Diesen Algorithmus jedoch so in das Programm einzubetten, dass er schnell genug lief, war eine Herausforderung. Da neben diesem Kernalgorithmus noch die Steuerungen fur die Servos und die Motoren laufen und andauernd die Steuerbe- ¨ fehle der Fernsteuerung eingelesen werden mussten, ist es wichtig, dass die Flugsteuerung Modular, also in vielen kleinen, einzeln aufrufbaren Programmfunktionen, implementiert ist. Auch diesen Aspekt habe ich zunächst etwas unterschätzt, konnte ihn letztendlich aber gut umsetzen.
Gerade die Verfugbarkeit von open source Software wie openScad [9] oder XFLR5 [10] hat ¨ dieses Projekt ermöglicht. Auch die heutzutage immer häufiger anzutreffenden Techniken,
wie 3D Druck oder CNC Fräsen, die eine gunstige Fertigung der Bauteile m ¨ | öglich machen,
unterstutzen den Forschungsprozess erheblich. Dar ¨ | uber hinaus gibt es gut dokumentierte, ¨
leistungsstarke Microcontroller, deren Finanzierung niemanden vor eine unuberwindbare ¨
Hurde stellen (das im roflCopter verwendete Teensy 3.2 Borad kostet ca. 20 ¨ | | e). So können
auch Schuler, wie ich, eigene Projektkonzepte in dieser Gr ¨ | | öße entwerfen und innerhalb ei-
nes uberschaubaren Preisrahmens (f ¨ | ur den roflCopter Version 2 ca. 200 ¨ | e) verwirklichen.
Einen Rotationsflugler habe ich anfangs f ¨ | ur dieses Projekt gew ¨ | ählt, da dieser Bereich
ziemlich unerforscht ist. Während des Projektes ist mir klar geworden, warum das so ist: Die Idee, mit einem Propeller einen Rotor anzutreiben, klingt zwar einleuchtend, ist aber alles andere als effizient. Schon ein einzelner Motor des roflCopters könnte diesen, bei einer Zugkraft von ca. 2N, problemlos hochheben und in der Luft halten. Da mir das Entwerfen und Bauen des Modells aber viel Spaß gemacht hat, ist mir das nicht weiter wichtig.
Zusammenfassend möchte ich festhalten, dass ich durch die Entwicklung dieses unkonventionell funktionierenden Fluggerätes mit einer eigenen, neuartigen Flugsteuerung sehr viel gelernt habe. Es mussen viele verschiedene Aspekte hinsichtlich Aerodynamik, Mechanik, ¨ sowie Fertigungs- und Materialtechniken berucksichtigt und die Software genau auf die ¨ Hardware abgestimmt werden. Die Ursprungliche Idee basierte zwar auf den beiden zu ¨ Beginn genannten Konzepten, letztendlich hat sich mit dem roflCopter daraus jedoch ein eigenes, neues Konzept entwickelt.

# Kapitel 6

# Verzeichnisse

## 6.1 Quellenverzeichnis

[1] Bildquelle: http://www.engadget.com/2008/09/15/wowwees-flytech-bladestar-can-governyour-home-autonomously/ (eingesehen am 07.05.2016)
[2] Bild extrahiert aus: https://www.youtube.com/watch?v=jtU1ZsjAqsE (eingesehen am 07.05.2016)
[3] http://robohub.org/the-monospinner-worlds-mechanically-simplest-controllable-flyingmachine/ (eingesehen am 06.05.2016)
[4] https://www.youtube.com/watch?v=ozp9e98BMhw (eingesehen am 15.01.2017)
[5] https://www.youtube.com/watch?v=sbuGCgc-JCM (eingesehen am 15.01.2017)
[6] https://www.youtube.com/watch?v=jtU1ZsjAqsE (eingesehen am 07.05.2016)
[7] https://hobbyking.com/de de/turnigytm-tgy-180d-180-degree-digital-servo-2-2kg-0-10sec-12g.html (eingesehen am 15.07.2017)
[8] http://www.mikrocontroller.net/articles/Datei:Servo.gif (eingesehen am 15.01.2017)
[9] http://www.openscad.org (eingesehen am 15.01.2017)
[10] http://www.xflr5.com/xflr5.htm (eingesehen am 15.01.2017)
[11] Eigene Aufnahme
[12] Bildschirmfoto der Software XFLR5
[13] Ausschnitt aus dem 3D Modell des RoflCopters Version 2
[14] Eigene Grafik
[15] Bildschirmfoto der Software Geogebra
[16] Grundlegende Erklärung zur Sensorfusion mithilfe des Kalman Filters: https://stanford.edu/class/ee267/lectures/lecture11.pdf (eingesehen am 23.02.2017)
[17] https://de.wikipedia.org/wiki/Pr%C3%A4zession (eingesehen am 24.02.2017)
[18] https://github.com/fr3dn3t/RoflCopter/tree/master/V2/videos (eingestellt am 14.02.2017)

## 6.2 Vielen Dank an:

Thomas Konnemann - Projektbetreuer. Christian Ambros - Unterstutzung bei physi- ¨ kalischen, mechanischen und softwaretechnischen Fragen. Jan Henrik Hemsing - Un-
terstutzung beim ¨ | Atzen der Platinen und Fragen zur Elektrotechnik ¨ | Jörg Frede - Bereit-
stellung seines 3D Druckers. Phillip Claves - Hilfe bei Fragen zur Firmwareentwicklung. Peter Auman - Fräsen der Rotorblätter. Dieter Dunschen - Fertigung der Steuerklappen. Die Friedensschule Munster ¨ - Finanzierung des Projektes.

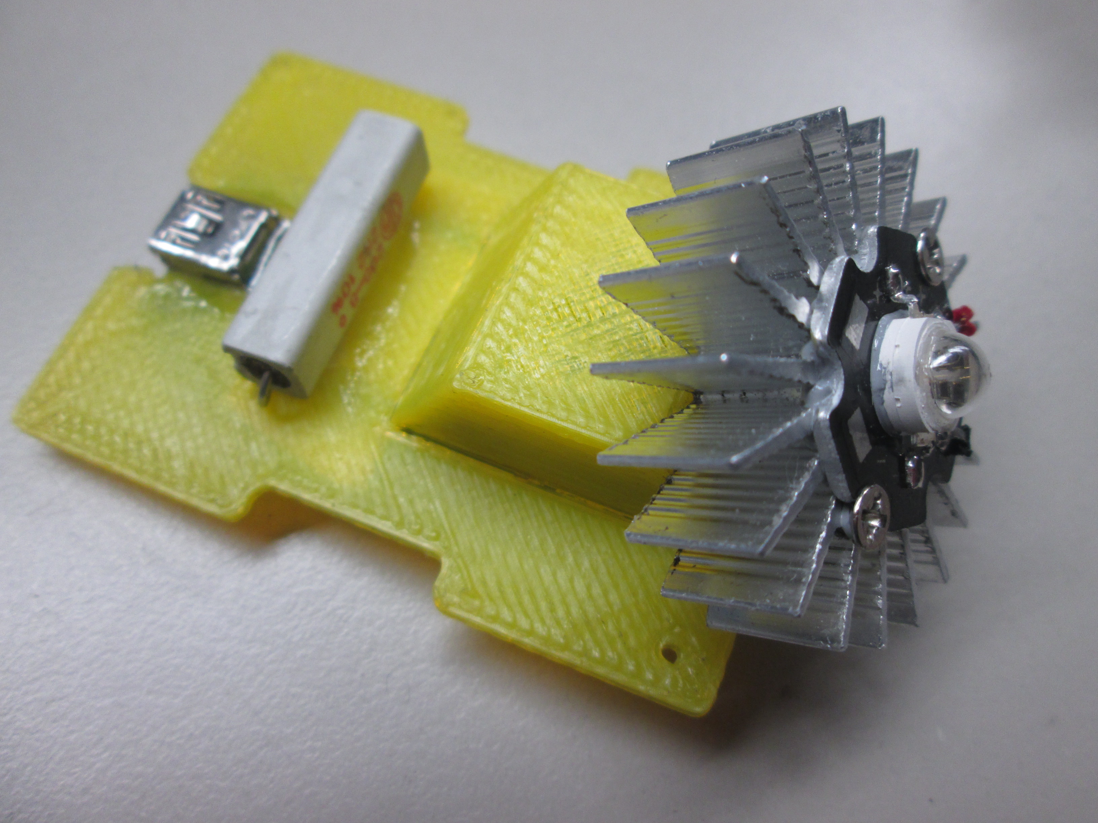
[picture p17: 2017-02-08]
irBeacon/images/jrModule.JPG

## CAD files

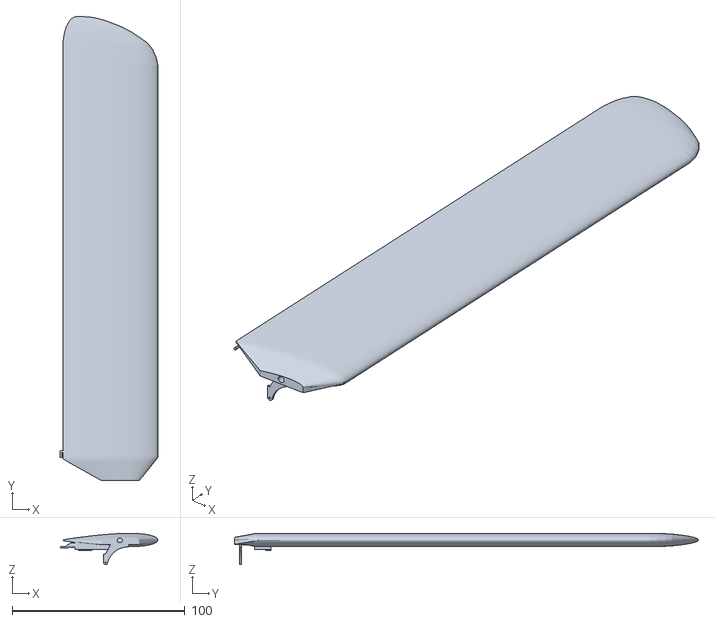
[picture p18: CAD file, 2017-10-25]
V3/3DFiles/rotorblade/rotorbladesOnly.stl
56.5 x 268.5 x 18.1

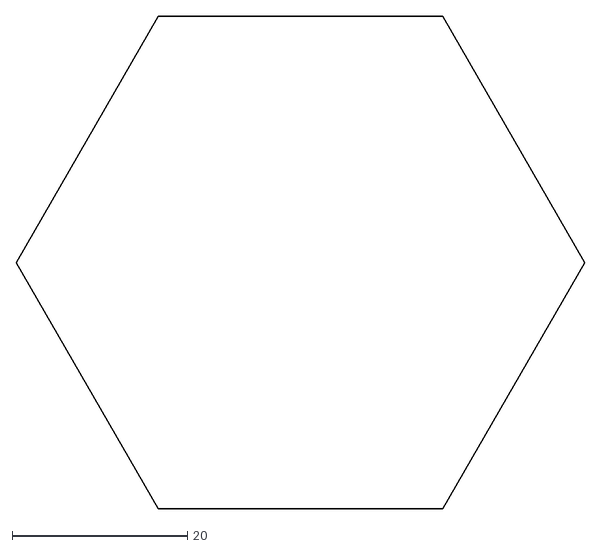
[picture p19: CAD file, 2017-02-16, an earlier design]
V2/3DFiles/simulationTemplates/hexagon.dxf
64.9 x 56.2

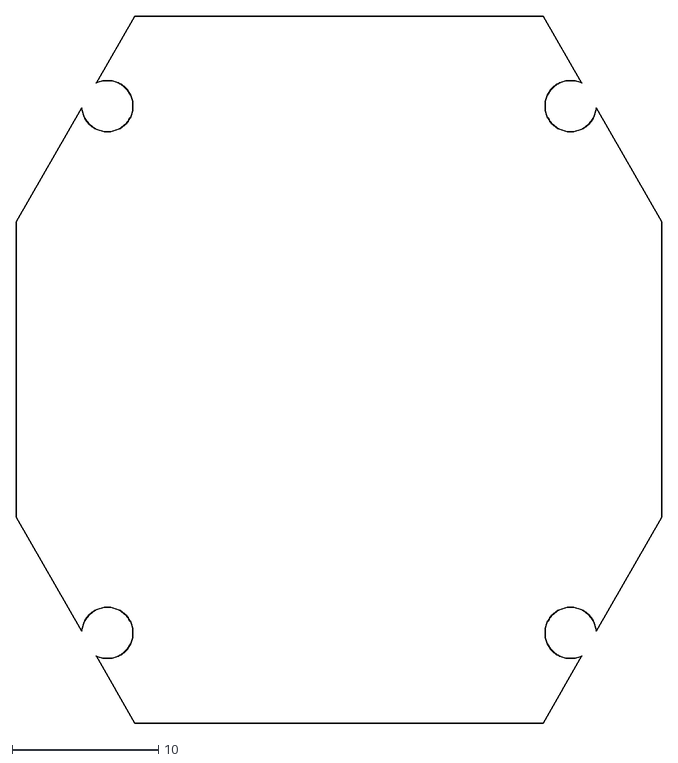
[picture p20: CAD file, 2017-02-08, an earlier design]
V2/pcb/platine/platine.dxf
44.1 x 48.3

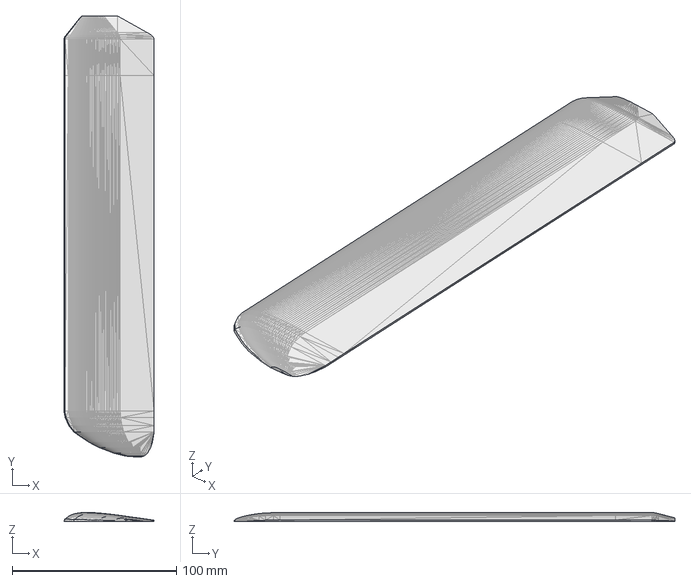
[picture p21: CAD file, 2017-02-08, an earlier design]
V2/rotorDesigns/rotorV01.step
55.0 x 268.5 x 5.51 mm

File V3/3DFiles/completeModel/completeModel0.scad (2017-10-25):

include <screwprop.scad>;
$fn = 2;
 //Servo
    //Servo Case
        servoLength = 23.15;
        servoWidth = 25.95;
        servoDepth = 12;
    //Servo Arm
        servoArmLength = 10;
        servoArmWidth = 3;
        servoArmThickness = 1;
    //Servo shaft
        servoShaftDiameter = 4;
        servoShaftHeight = 10;
        servoShaftOffset = 4;
        
        servoOffset = 2.5;
        
//PCB
    pcbHeight = 1.5;
    spaceUnderPCB = 1;
//IMU
    imuLength = 20.5;
    imuWidth = 10.5;
    imuHeight = 2;
 
//RadioReciever
    recieverLength = 25;
    recieverWidth = 12;
    recieverHeight = 2;
    
//2.4ghz serial
    serialLength = 18.5;
    serialWidth = 13.5;
    serialHeight = 2;
    
//mount plate
    mountPlateHeight = 9;
    motorArmGapSpace = 0.25;
    
//servoMount
    showServoMount = true;
        
//motor arm
    motorArmThickness = 6;
    motorArmLength = 320;
    
//bladeGear
    bladeGearDiameter = 4.2;
    bladeGearLength = 16.5;
    
    bladeGearFixingRingHeight = 5.5;
    bladeGearFixingRingDiameter = 8.35;
    
//  PinHeader
    pinHeaderWidth = 1.6;
    pinHeaderLength = 36;
    pinHeaderHeight = 9.32;
    pinHeaderOffset = 6.2;
    
//DIPFORTy1
    DIPFORTy1Length =   51; 
    DIPFORTy1Width  =   18;
    DIPFORTy1Height =   1.2;
    
//rotor
    rotorWidth = 55;
    
//motorMount
    motorDiameter = 13;
    motorMountLength = 30;
    
//bumper
    bumperPosX = servoWidth*0.61;
    bumperPosY = 18;
    showBumper = false;
    
    bumperHole = 3.5;
    
//tsop
    showTsopBottom = false;
    
//solenoid arm
    steelDia = 1.3;
    width = 3.3;
    innerWidth = 1.2;

    depth = 5;
    gapDepth = 2.8;

module foil(translateY, translateX, x, foilLength) {
    translate([translateX,-translateY,0]) {
        rotate([90,0,0]) {   
            linear_extrude(foilLength) {
                polygon(points=[
                    [x*	1.00000	, x*	0.00147	],
                    [x*	0.99280	, x*	0.00264	],
                    [x*	0.97989	, x*	0.00472	],
                    [x*	0.96352	, x*	0.00731	],
                    [x*	0.94455	, x*	0.01025	],
                    [x*	0.92350	, x*	0.01343	],
                    [x*	0.90075	, x*	0.01678	],
                    [x*	0.87658	, x*	0.02025	],
                    [x*	0.85123	, x*	0.02378	],
                    [x*	0.82489	, x*	0.02734	],
                    [x*	0.79774	, x*	0.03090	],
                    [x*	0.76991	, x*	0.03442	],
                    [x*	0.74154	, x*	0.03789	],
                    [x*	0.71275	, x*	0.04129	],
                    [x*	0.68365	, x*	0.04458	],
                    [x*	0.65434	, x*	0.04775	],
                    [x*	0.62492	, x*	0.05079	],
                    [x*	0.59547	, x*	0.05367	],
                    [x*	0.56607	, x*	0.05638	],
                    [x*	0.53680	, x*	0.05889	],
                    [x*	0.50774	, x*	0.06119	],
                    [x*	0.47895	, x*	0.06326	],
                    [x*	0.45050	, x*	0.06508	],
                    [x*	0.42246	, x*	0.06664	],
                    [x*	0.39488	, x*	0.06792	],
                    [x*	0.36782	, x*	0.06891	],
                    [x*	0.34135	, x*	0.06959	],
                    [x*	0.31551	, x*	0.06996	],
                    [x*	0.29035	, x*	0.07000	],
                    [x*	0.26594	, x*	0.06970	],
                    [x*	0.24231	, x*	0.06907	],
                    [x*	0.21951	, x*	0.06809	],
                    [x*	0.19760	, x*	0.06677	],
                    [x*	0.17661	, x*	0.06511	],
                    [x*	0.15660	, x*	0.06312	],
                    [x*	0.13760	, x*	0.06079	],
                    [x*	0.11965	, x*	0.05814	],
                    [x*	0.10280	, x*	0.05518	],
                    [x*	0.08709	, x*	0.05191	],
                    [x*	0.07256	, x*	0.04836	],
                    [x*	0.05924	, x*	0.04454	],
                    [x*	0.04717	, x*	0.04045	],
                    [x*	0.03639	, x*	0.03612	],
                    [x*	0.02694	, x*	0.03156	],
                    [x*	0.01885	, x*	0.02678	],
                    [x*	0.01215	, x*	0.02180	],
                    [x*	0.00688	, x*	0.01662	],
                    [x*	0.00308	, x*	0.01126	],
                    [x*	0.00078	, x*	0.00572	],
                    [x*	0.00000	, x*	0.00000	],
                    [x*	0.00078	, x*	-0.00572	],
                    [x*	0.00308	, x*	-0.01126	],
                    [x*	0.00688	, x*	-0.01662	],
                    [x*	0.01215	, x*	-0.02180	],
                    [x*	0.01885	, x*	-0.02678	],
                    [x*	0.02694	, x*	-0.03156	],
                    [x*	0.03639	, x*	-0.03612	],
                    [x*	0.04717	, x*	-0.04045	],
                    [x*	0.05924	, x*	-0.04454	],
                    [x*	0.07256	, x*	-0.04836	],
                    [x*	0.08709	, x*	-0.05191	],
                    [x*	0.10280	, x*	-0.05518	],
                    [x*	0.11965	, x*	-0.05814	],
                    [x*	0.13760	, x*	-0.06079	],
                    [x*	0.15660	, x*	-0.06312	],
                    [x*	0.17661	, x*	-0.06511	],
                    [x*	0.19760	, x*	-0.06677	],
                    [x*	0.21951	, x*	-0.06809	],
                    [x*	0.24231	, x*	-0.06907	],
                    [x*	0.26594	, x*	-0.06970	],
                    [x*	0.29035	, x*	-0.07000	],
                    [x*	0.31551	, x*	-0.06996	],
                    [x*	0.34135	, x*	-0.06959	],
                    [x*	0.36782	, x*	-0.06891	],
                    [x*	0.39488	, x*	-0.06792	],
                    [x*	0.42246	, x*	-0.06664	],
                    [x*	0.45050	, x*	-0.06508	],
                    [x*	0.47895	, x*	-0.06326	],
                    [x*	0.50774	, x*	-0.06119	],
                    [x*	0.53680	, x*	-0.05889	],
                    [x*	0.56607	, x*	-0.05638	],
                    [x*	0.59547	, x*	-0.05367	],
                    [x*	0.62492	, x*	-0.05079	],
                    [x*	0.65434	, x*	-0.04775	],
                    [x*	0.68365	, x*	-0.04458	],
                    [x*	0.71275	, x*	-0.04129	],
                    [x*	0.74154	, x*	-0.03789	],
                    [x*	0.76991	, x*	-0.03442	],
                    [x*	0.79774	, x*	-0.03090	],
                    [x*	0.82489	, x*	-0.02734	],
                    [x*	0.85123	, x*	-0.02378	],
                    [x*	0.87658	, x*	-0.02025	],
                    [x*	0.90075	, x*	-0.01678	],
                    [x*	0.92350	, x*	-0.01343	],
                    [x*	0.94455	, x*	-0.01025	],
                    [x*	0.96352	, x*	-0.00731	],
                    [x*	0.97989	, x*	-0.00472	],
                    [x*	0.99280	, x*	-0.00264	],
                    [x*	1.00000	, x*	-0.00147	]
                ]);
            }
        }
    }
}

module prop() {
    mirror([1,0,0]) {screwprop(33, 4.5, 20, 5.5);}
    mirror([1,0,0]) {rotate(a=[0,90,0])  {screwprop(33, 4.5, 20, 5.5);};}
    mirror([1,0,0]) {rotate(a=[0,180,0]) {screwprop(33, 4.5,  20, 5.5);};}
    mirror([1,0,0]) {rotate(a=[0,270,0]) {screwprop(33, 4.5, 20, 5.5);};}


        difference() {
            union() {
                translate([0,2.3,0])rotate(a=[90,0,0]) cylinder(h = 6.7, r=5.1, $fn=70);
                translate([0,2.5,0])rotate(a=[90,0,0]) cylinder(h = 7, r=4.8, $fn=70);
            }
            translate([0,2.5,0])rotate(a=[90,0,0]) cylinder(h = 7, r=2, $fn=70);
        }

    translate([0,2.2,0]) {
        rotate([90,0,0]) {
            rotate_extrude(convexity = 10)
                translate([10.2/2-0.3, 0, 0])
                    circle(r = 0.3);
        }
    }

    translate([0,3,0]) {
        rotate([90,0,0]) {
            cylinder(d=9.4, h=0.7);
            translate([0,0,0]) {
                difference() {
                    resize(newsize=[8.5,8.5,16]) sphere(r=30);
                    translate([0,0,10]) {
                      cube([20,20,20],center=true);
                    }
                }
            }
        }
    }
}

module motor() {
    difference() {
        cylinder(d1=16, d2=17.5, h=4);
        translate([7.5,0,0]) {
            cylinder(d=8,h=3.85);
        }
        translate([-7.5,0,0]) {
            cylinder(d=8,h=3.85);
        }
        translate([0,7.5,0]) {
            cylinder(d=8,h=3.85);
        }
        translate([0,-7.5,0]) {
            cylinder(d=8,h=3.85);
        }
        translate([0,0,3.85]) {
            cylinder(d=15, h=0.15);
        }
    }
    translate([0,0,4.1]) {
        cylinder(d=17.5, h=6);
    }
    translate([0,0,10.1]) {
        cylinder(d1=17.5, d2=14, h=2);
    }
}
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

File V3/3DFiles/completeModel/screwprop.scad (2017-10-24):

module screwprop(radius, inside_radius, pitch, chord)
{
rad_res = 25;
chord_res = 25;
chord_cmass = 40;  // As a percent of cord, specifies the center of mass of the section.
thick_cmass = 5;   // As a percent of chord, specifies the center of mass of the section.

// Describes the upper surface as a percent of chord
function top_foil(p) = lookup(p, [
		[0, 0 ],
		[1.25, .04 ],
		[2.5, .0579],
		[5, .082],
		[7.5, .1 ],
            [10, .1138],
            [15, .13],
            [20, .1385],
            [25, .1429],
            [30, .1418],
            [35, .1384],
            [40, .1321],
            [50, .1129],
            [60, .0894],
            [70, .0622],
            [80, .0378],
            [90, .0157],
            [100, 0] 
	]);

// Describes the lower surface as a percent of chort
function bottom_foil(p) = lookup(p, [
		[0,0 ],
		[5, -.03 ],
		[10, -.04 ],
		[ 50, -.03 ],
		[ 100, 0 ]
	]);

// Modifies chord as a function of radius
function chord_modifier(p) = lookup(p, [
		[0, 1 ],
    [50, 1],
		[100, .6]
	]);  
	
// Modifies thickness as a function of radius
function thick_modifier(p) = lookup(p, [
		[0, 2 ],
            [50, 1],
		[100, 1]
	]); 
	 
// Angle of attack as a function of radius
function attack_modifier(p) = lookup(p, [
		[0, 0 ],
            [50, 0],
		[100, 0]
	]); 

// Internal variables
// First inside vars, scaled
x1=0; x2=0; // x must be slow axis
y11=0; y12=0;  y21=0; y22=0;
z11t=0; z12t=0;  z21t=0; z22t=0;
z11b=0; z12b=0;  z21b=0; z22b=0;
xtable1 = 0; xtable2 = 0;  // for table look up
ytable1 = 0; ytable2 = 0;  // for table look up
zoffset1 = 0; zoffset2 = 0;   // For center of mass adjustment

// First inside vars, scaled
ang1 = 0; ang2 = 0;

// Third inside vars
cos1 = 0; cos2 = 0; sin1 = 0; sin2 = 0;

// Forth inside vars
p0  = [0,0,0]; p1 = [0,0,0];p2  = [0,0,0]; p3 = [0,0,0];
p4  = [0,0,0]; p5 = [0,0,0];p6  = [0,0,0]; p7 = [0,0,0];

for ( x = [0:rad_res-1], y = [0:chord_res-1]) {
assign(    x1 = inside_radius+(radius - inside_radius)*(x/(rad_res)), 
           x2 =  inside_radius+(radius - inside_radius)*((x+1)/(rad_res))){

assign(    xtable1 = x1 *100  / radius,
           xtable2 = x2 *100  /radius,
           ytable1 = y*100/chord_res,
           ytable2 = (y+1)*100/chord_res){

assign(    ang1 = atan(x1*3.14159*2/pitch) - attack_modifier(xtable1), 
           ang2 = atan(x2*3.14159*2/pitch) - attack_modifier(xtable2),
           zoffset1 = -chord*thick_cmass*chord_modifier(xtable1)* thick_modifier(xtable1)/100,
           zoffset2 =- chord*thick_cmass*chord_modifier(xtable2)* thick_modifier(xtable2)/100){
           
assign(    cos1 = cos(ang1), cos2 = cos(ang2), 
           sin1 = sin(ang1), sin2 = sin(ang2),
           y11=chord_cmass*chord*chord_modifier(xtable1)/100 -  y*chord*chord_modifier(xtable1)/chord_res,
           y12=chord_cmass*chord*chord_modifier(xtable1)/100 - (y+1)*chord*chord_modifier(xtable1)/chord_res,
           y21=chord_cmass*chord*chord_modifier(xtable2)/100 -  y*chord*chord_modifier(xtable2)/chord_res, 
           y22=chord_cmass*chord*chord_modifier(xtable2)/100  - (y+1)*chord*chord_modifier(xtable2)/chord_res,
           z11t = zoffset1 + chord*chord_modifier(xtable1)*top_foil(ytable1)* thick_modifier(xtable1),
           z12t = zoffset1 + chord*chord_modifier(xtable1)*top_foil(ytable2)* thick_modifier(xtable1),
           z21t = zoffset2 + chord*chord_modifier(xtable2)*top_foil(ytable1)* thick_modifier(xtable2),
           z22t = zoffset2 + chord*chord_modifier(xtable2)*top_foil(ytable2)* thick_modifier(xtable2),          
           z11b = zoffset1 + chord*chord_modifier(xtable1)*bottom_foil(ytable1)* thick_modifier(xtable1),
           z12b = zoffset1 + chord*chord_modifier(xtable1)*bottom_foil(ytable2)* thick_modifier(xtable1),
           z21b = zoffset2 + chord*chord_modifier(xtable2)*bottom_foil(ytable1)* thick_modifier(xtable2),
           z22b = zoffset2 + chord*chord_modifier(xtable2)*bottom_foil(ytable2)* thick_modifier(xtable2)){

assign(   // rotational transform
           p0 = [x1, y11*cos1 + z11t*sin1, z11t*cos1 - y11*sin1],
           p1 = [x1, y12*cos1 + z12t*sin1, z12t*cos1 - y12*sin1],
           p2 = [x1, y11*cos1 + z11b*sin1, z11b*cos1 - y11*sin1],
           p3 = [x1, y12*cos1 + z12b*sin1, z12b*cos1 - y12*sin1],
           p4 = [x2, y21*cos2 + z21t*sin2, z21t*cos2 - y21*sin2],
           p5 = [x2, y22*cos2 + z22t*sin2, z22t*cos2 - y22*sin2],
           p6 = [x2, y21*cos2 + z21b*sin2, z21b*cos2 - y21*sin2],
           p7 = [x2, y22*cos2 + z22b*sin2, z22b*cos2 - y22*sin2]
){  
if(x == 0) {

    polyhedron
    (points = [p0, p1, p2, p3, p4, p5, p6, p7],
     triangles =  [
                 [0,1,2],  [2,1,3],  // inside endcap
            //    [4,6,5], [5,6,7],  // outside endcap
            //      [0,2,4],[2,4,6],[1,5,3],[7,5,3],    // interiors, not used ever
                    [0,4,5],[1,0,5],[2,3,6],[6,3,7]   // main surfaces
                  ]
     );  // end poly

} else{

  if(x==rad_res-1) {

    polyhedron
    (points = [p0, p1, p2, p3, p4, p5, p6, p7],
     triangles =  [
             //    [0,1,2],  [2,1,3],  // inside endcap
                [4,6,5], [5,6,7],  // outside endcap
            //      [0,2,4],[2,4,6],[1,5,3],[7,5,3],    // interiors, not used ever
                    [0,4,5],[1,0,5],[2,3,6],[6,3,7]   // main surfaces
                  ]
     );  // end poly

} else {

    polyhedron
    (points = [p0, p1, p2, p3, p4, p5, p6, p7],
     triangles =  [
             //    [0,1,2],  [2,1,3],  // inside endcap
            //    [4,6,5], [5,6,7],  // outside endcap
            //      [0,2,4],[2,4,6],[1,5,3],[7,5,3],    // interiors, not used ever
                    [0,4,5],[1,0,5],[2,3,6],[6,3,7]   // main surfaces
                  ]
     );  // end poly

  }
}

  }  // end assign
  }  // end assign
  }  // end assign
  }  // end assign
  }  // end assign  
};  // end for


};   // end module


////////////////////////////////
////////////////////////////////

   //   screwprop(12, 3, 20, 2.5);

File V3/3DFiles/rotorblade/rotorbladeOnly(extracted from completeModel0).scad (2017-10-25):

include <screwprop.scad>;
$fn = 90;
 //Servo
    //Servo Case
        servoLength = 23.15;
        servoWidth = 25.95;
        servoDepth = 12;
    //Servo Arm
        servoArmLength = 10;
        servoArmWidth = 3;
        servoArmThickness = 1;
    //Servo shaft
        servoShaftDiameter = 4;
        servoShaftHeight = 10;
        servoShaftOffset = 4;
        
        servoOffset = 2.5;
        
//PCB
    pcbHeight = 1.5;
    spaceUnderPCB = 1;
//IMU
    imuLength = 20.5;
    imuWidth = 10.5;
    imuHeight = 2;
 
//RadioReciever
    recieverLength = 25;
    recieverWidth = 12;
    recieverHeight = 2;
    
//2.4ghz serial
    serialLength = 18.5;
    serialWidth = 13.5;
    serialHeight = 2;
    
//mount plate
    mountPlateHeight = 9;
    motorArmGapSpace = 0.25;
    
//servoMount
    showServoMount = true;
        
//motor arm
    motorArmThickness = 6;
    motorArmLength = 320;
    
//bladeGear
    bladeGearDiameter = 4.2;
    bladeGearLength = 16.5;
    
    bladeGearFixingRingHeight = 5.5;
    bladeGearFixingRingDiameter = 8.35;
    
//  PinHeader
    pinHeaderWidth = 1.6;
    pinHeaderLength = 36;
    pinHeaderHeight = 9.32;
    pinHeaderOffset = 6.2;
    
//DIPFORTy1
    DIPFORTy1Length =   51; 
    DIPFORTy1Width  =   18;
    DIPFORTy1Height =   1.2;
    
//rotor
    rotorWidth = 55;
    
//motorMount
    motorDiameter = 13;
    motorMountLength = 30;
    
//bumper
    bumperPosX = servoWidth*0.61;
    bumperPosY = 18;
    showBumper = false;
    
    bumperHole = 3.5;
    
//tsop
    showTsopBottom = false;
    
//solenoid arm
    steelDia = 1.3;
    width = 3.3;
    innerWidth = 1.2;

    depth = 5;
    gapDepth = 2.8;

module foil(translateY, translateX, x, foilLength) {
    translate([translateX,-translateY,0]) {
        rotate([90,0,0]) {   
            linear_extrude(foilLength) {
                polygon(points=[
                    [x*	1.00000	, x*	0.00147	],
                    [x*	0.99280	, x*	0.00264	],
                    [x*	0.97989	, x*	0.00472	],
                    [x*	0.96352	, x*	0.00731	],
                    [x*	0.94455	, x*	0.01025	],
                    [x*	0.92350	, x*	0.01343	],
                    [x*	0.90075	, x*	0.01678	],
                    [x*	0.87658	, x*	0.02025	],
                    [x*	0.85123	, x*	0.02378	],
                    [x*	0.82489	, x*	0.02734	],
                    [x*	0.79774	, x*	0.03090	],
                    [x*	0.76991	, x*	0.03442	],
                    [x*	0.74154	, x*	0.03789	],
                    [x*	0.71275	, x*	0.04129	],
                    [x*	0.68365	, x*	0.04458	],
                    [x*	0.65434	, x*	0.04775	],
                    [x*	0.62492	, x*	0.05079	],
                    [x*	0.59547	, x*	0.05367	],
                    [x*	0.56607	, x*	0.05638	],
                    [x*	0.53680	, x*	0.05889	],
                    [x*	0.50774	, x*	0.06119	],
                    [x*	0.47895	, x*	0.06326	],
                    [x*	0.45050	, x*	0.06508	],
                    [x*	0.42246	, x*	0.06664	],
                    [x*	0.39488	, x*	0.06792	],
                    [x*	0.36782	, x*	0.06891	],
                    [x*	0.34135	, x*	0.06959	],
                    [x*	0.31551	, x*	0.06996	],
                    [x*	0.29035	, x*	0.07000	],
                    [x*	0.26594	, x*	0.06970	],
                    [x*	0.24231	, x*	0.06907	],
                    [x*	0.21951	, x*	0.06809	],
                    [x*	0.19760	, x*	0.06677	],
                    [x*	0.17661	, x*	0.06511	],
                    [x*	0.15660	, x*	0.06312	],
                    [x*	0.13760	, x*	0.06079	],
                    [x*	0.11965	, x*	0.05814	],
                    [x*	0.10280	, x*	0.05518	],
                    [x*	0.08709	, x*	0.05191	],
                    [x*	0.07256	, x*	0.04836	],
                    [x*	0.05924	, x*	0.04454	],
                    [x*	0.04717	, x*	0.04045	],
                    [x*	0.03639	, x*	0.03612	],
                    [x*	0.02694	, x*	0.03156	],
                    [x*	0.01885	, x*	0.02678	],
                    [x*	0.01215	, x*	0.02180	],
                    [x*	0.00688	, x*	0.01662	],
                    [x*	0.00308	, x*	0.01126	],
                    [x*	0.00078	, x*	0.00572	],
                    [x*	0.00000	, x*	0.00000	],
                    [x*	0.00078	, x*	-0.00572	],
                    [x*	0.00308	, x*	-0.01126	],
                    [x*	0.00688	, x*	-0.01662	],
                    [x*	0.01215	, x*	-0.02180	],
                    [x*	0.01885	, x*	-0.02678	],
                    [x*	0.02694	, x*	-0.03156	],
                    [x*	0.03639	, x*	-0.03612	],
                    [x*	0.04717	, x*	-0.04045	],
                    [x*	0.05924	, x*	-0.04454	],
                    [x*	0.07256	, x*	-0.04836	],
                    [x*	0.08709	, x*	-0.05191	],
                    [x*	0.10280	, x*	-0.05518	],
                    [x*	0.11965	, x*	-0.05814	],
                    [x*	0.13760	, x*	-0.06079	],
                    [x*	0.15660	, x*	-0.06312	],
                    [x*	0.17661	, x*	-0.06511	],
                    [x*	0.19760	, x*	-0.06677	],
                    [x*	0.21951	, x*	-0.06809	],
                    [x*	0.24231	, x*	-0.06907	],
                    [x*	0.26594	, x*	-0.06970	],
                    [x*	0.29035	, x*	-0.07000	],
                    [x*	0.31551	, x*	-0.06996	],
                    [x*	0.34135	, x*	-0.06959	],
                    [x*	0.36782	, x*	-0.06891	],
                    [x*	0.39488	, x*	-0.06792	],
                    [x*	0.42246	, x*	-0.06664	],
                    [x*	0.45050	, x*	-0.06508	],
                    [x*	0.47895	, x*	-0.06326	],
                    [x*	0.50774	, x*	-0.06119	],
                    [x*	0.53680	, x*	-0.05889	],
                    [x*	0.56607	, x*	-0.05638	],
                    [x*	0.59547	, x*	-0.05367	],
                    [x*	0.62492	, x*	-0.05079	],
                    [x*	0.65434	, x*	-0.04775	],
                    [x*	0.68365	, x*	-0.04458	],
                    [x*	0.71275	, x*	-0.04129	],
                    [x*	0.74154	, x*	-0.03789	],
                    [x*	0.76991	, x*	-0.03442	],
                    [x*	0.79774	, x*	-0.03090	],
                    [x*	0.82489	, x*	-0.02734	],
                    [x*	0.85123	, x*	-0.02378	],
                    [x*	0.87658	, x*	-0.02025	],
                    [x*	0.90075	, x*	-0.01678	],
                    [x*	0.92350	, x*	-0.01343	],
                    [x*	0.94455	, x*	-0.01025	],
                    [x*	0.96352	, x*	-0.00731	],
                    [x*	0.97989	, x*	-0.00472	],
                    [x*	0.99280	, x*	-0.00264	],
                    [x*	1.00000	, x*	-0.00147	]
                ]);
            }
        }
    }
}

/*
module prop() {
    mirror([1,0,0]) {screwprop(33, 4.5, 20, 5.5);}
    mirror([1,0,0]) {rotate(a=[0,90,0])  {screwprop(33, 4.5, 20, 5.5);};}
    mirror([1,0,0]) {rotate(a=[0,180,0]) {screwprop(33, 4.5,  20, 5.5);};}
    mirror([1,0,0]) {rotate(a=[0,270,0]) {screwprop(33, 4.5, 20, 5.5);};}


        difference() {
            union() {
                translate([0,2.3,0])rotate(a=[90,0,0]) cylinder(h = 6.7, r=5.1, $fn=70);
                translate([0,2.5,0])rotate(a=[90,0,0]) cylinder(h = 7, r=4.8, $fn=70);
            }
            translate([0,2.5,0])rotate(a=[90,0,0]) cylinder(h = 7, r=2, $fn=70);
        }

    translate([0,2.2,0]) {
        rotate([90,0,0]) {
            rotate_extrude(convexity = 10)
                translate([10.2/2-0.3, 0, 0])
                    circle(r = 0.3);
        }
    }

    translate([0,3,0]) {
        rotate([90,0,0]) {
            cylinder(d=9.4, h=0.7);
            translate([0,0,0]) {
                difference() {
                    resize(newsize=[8.5,8.5,16]) sphere(r=30);
                    translate([0,0,10]) {
                      cube([20,20,20],center=true);
                    }
                }
            }
        }
    }
}

module motor() {
    difference() {
        cylinder(d1=16, d2=17.5, h=4);
        translate([7.5,0,0]) {
            cylinder(d=8,h=3.85);
        }
        translate([-7.5,0,0]) {
            cylinder(d=8,h=3.85);
        }
        translate([0,7.5,0]) {
            cylinder(d=8,h=3.85);
        }
        translate([0,-7.5,0]) {
            cylinder(d=8,h=3.85);
        }
        translate([0,0,3.85]) {
            cylinder(d=15, h=0.15);
        }
    }
    translate([0,0,4.1]) {
        cylinder(d=17.5, h=6);
    }
    translate([0,0,10.1]) {
        cylinder(d1=17.5, d2=14, h=2);
    }
}
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

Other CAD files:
V3/3DFiles/rotorblade/bladeNACA0012.scad
V1/3DFiles/motorMount.scad
V2/3DFiles/bumper/bumper.scad
V2/3DFiles/bumper/bumperForm.scad
V2/3DFiles/completeModel/completeModel.scad
V2/3DFiles/completeModel/completeModelnew.scad
V2/3DFiles/completeModel/completeModelnew2.scad
V2/3DFiles/completeModel/completeModelnew3.scad
V2/3DFiles/completeModel/completeModelnew4.scad
V2/3DFiles/completeModel/completeModelnew5.scad
V2/3DFiles/flap/klappe.scad
V2/3DFiles/ir/irTest.scad
V2/3DFiles/ir/tsop.scad
V2/3DFiles/motorMount/motorMount.scad
V2/3DFiles/propAdapter/propAdapter.scad
V2/3DFiles/propAdapter/propAdapter4blade.scad
V2/3DFiles/rotorMount/rotorAnsatz.scad
V2/3DFiles/rotorMount/ruderhorn.scad
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

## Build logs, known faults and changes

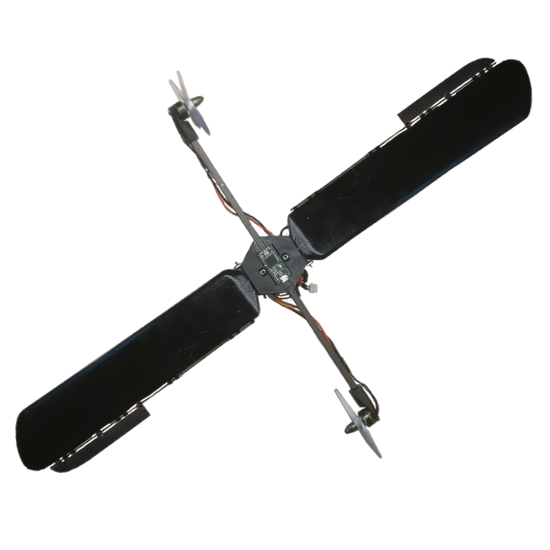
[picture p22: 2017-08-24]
Software/flapDebug/copterFree2.png

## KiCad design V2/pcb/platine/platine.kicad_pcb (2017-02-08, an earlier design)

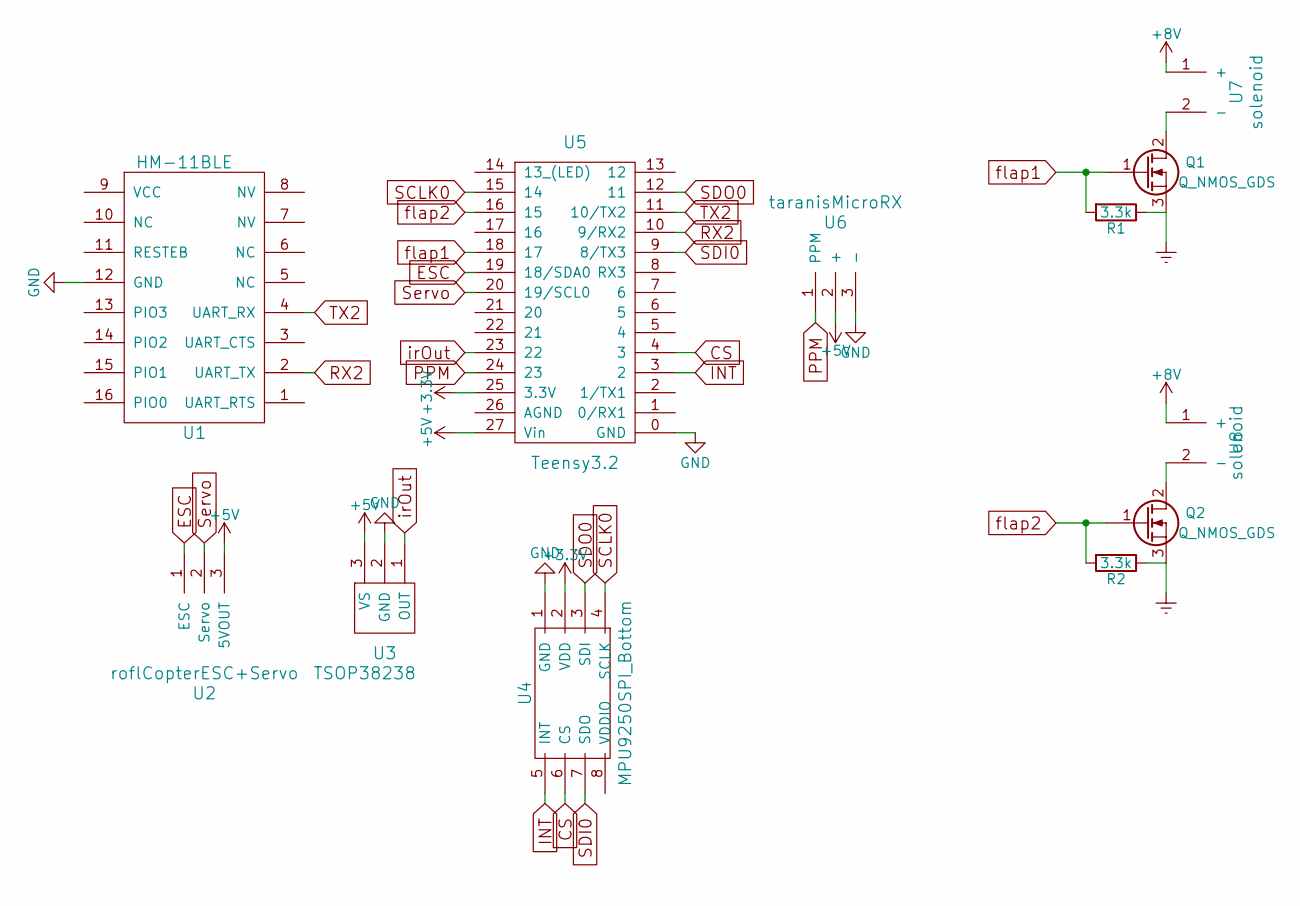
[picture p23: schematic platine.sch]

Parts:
Q1, Q2: Q_NMOS_GDS; TO-252-2Lead
R1, R2: 3.3k; R_1206_HandSoldering
U1: HM-11BLE; HM-11ble
U2: roflCopterESC+Servo
U3: TSOP38238
U4: MPU9250SPI_Bottom; MPU9250SPI_BOTTOM
U5: Teensy3.2; Teensy3.2_l
U6: taranisMicroRX
U7, U8: solenoid

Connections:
+3V3: U4.2 (VDD), U5.25 (3.3V)
+5V: U2.3 (5VOUT), U3.3 (VS), U5.27 (Vin), U6.2 (+)
+8V: U7.1 (+), U8.1 (+)
CS: U4.6 (CS), U5.4 (3)
ESC: U2.1 (ESC), U5.19 (18/SDA0)
Earth: Q1.3 (S), Q2.3 (S), R1.1, R2.1
GND: U1.12 (GND), U3.2 (GND), U4.1 (GND), U5.0 (GND), U6.3 (-)
INT: U4.5 (INT), U5.3 (2)
unnamed: Q1.2 (D), U7.2 (-)
unnamed: Q2.2 (D), U8.2 (-)
PPM: U5.24 (23), U6.1 (PPM)
RX2: U1.2 (UART_TX), U5.10 (9/RX2)
SCLK0: U4.4 (SCLK), U5.15 (14)
SDI0: U4.7 (SDO), U5.9 (8/TX3)
SDO0: U4.3 (SDI), U5.12 (11)
Servo: U2.2 (Servo), U5.20 (19/SCL0)
TX2: U1.4 (UART_RX), U5.11 (10/TX2)
flap1: Q1.1 (G), R1.2, U5.18 (17)
flap2: Q2.1 (G), R2.2, U5.16 (15)
irOut: U3.1 (OUT), U5.23 (22)

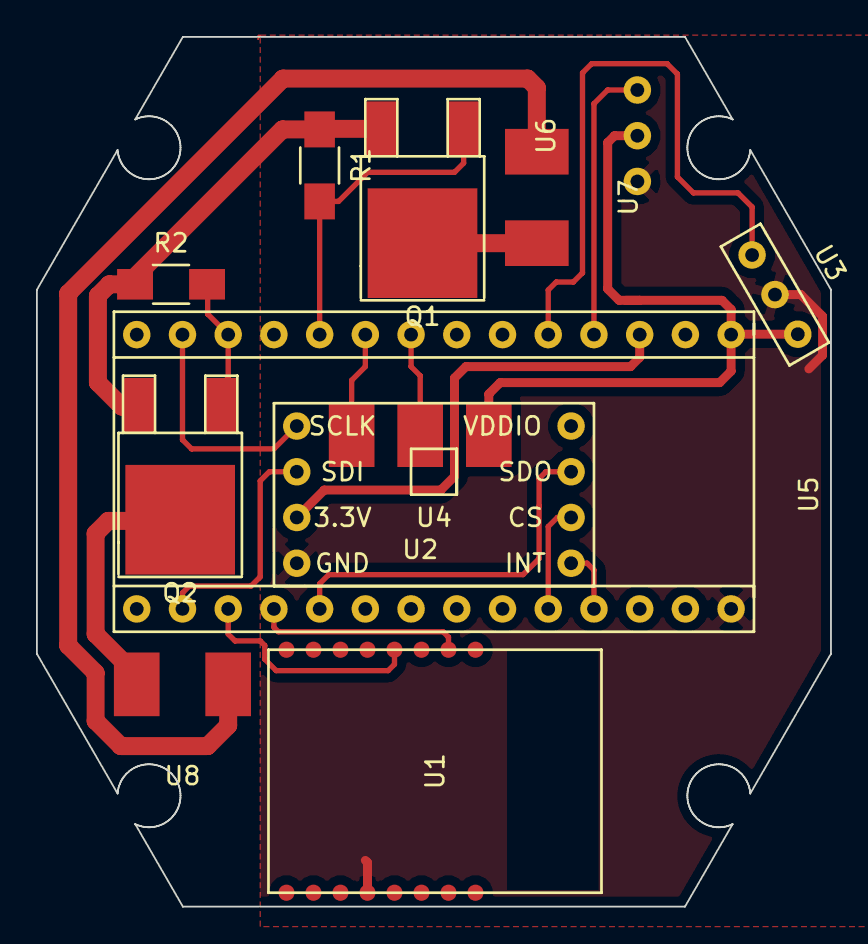
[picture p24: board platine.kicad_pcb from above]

Board: 2 copper layers, 44.1 x 48.3 mm, 12 parts (0 on the bottom side), 20 nets.

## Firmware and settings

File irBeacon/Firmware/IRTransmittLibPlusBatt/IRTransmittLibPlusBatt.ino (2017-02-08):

#include <IRcontinuous.h>

int ledPin = 6;


int irPin = 27;
int tonePin = 0;
int beepCounter = 0;


IRsend irsend;

boolean ledOn=false;
void setup() {
  Serial.begin(9600);

  pinMode(ledPin, OUTPUT);
  pinMode(irPin, OUTPUT);

  digitalWrite(irPin, LOW);
  digitalWrite(ledPin, HIGH);
  
  delay(5000);
  tone(tonePin, 800);       // Begin the tone
  delay(500);
  noTone(tonePin);
  
  delay(500);
  tone(tonePin, 800);       // Begin the tone
  delay(500);
  noTone(tonePin);
  
  delay(500);
  tone(tonePin, 1200);       // Begin the tone
  delay(700);
  noTone(tonePin);
}

void loop() {
  //sendRaw(int peak, int lengh, int hz)
  irsend.sendRaw(400, 100, 38);

  //Let the led blink to indicate active status
  if(ledOn) {
    ledOn = false;
    digitalWrite(ledPin, LOW);
  }
  else {
    ledOn = true;
    digitalWrite(ledPin, HIGH);
  }

  //a beep every x seconds to indicate active status
  //clear the tone when counter was reset
  if(beepCounter==0) {
    noTone(tonePin);
  }
  
  beepCounter++;

  //activete tone and reset counter when round x was passed
  if(beepCounter > 200) {
    beepCounter=0;
    tone(tonePin, 1200);
  }
  //delay(1500); //In this example, the signal will be repeated every 1.5 seconds, approximately.
}

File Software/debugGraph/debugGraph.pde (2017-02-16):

String stringKalmanX, stringKalmanY, stringRPM;

final int width = 1280;
final int height = 800;

float[] kalmanX;
float[] kalmanY;
float[] rpm;

float angleX = 0.00, angleY = 0.00;

boolean drawValues  = false;

int rectX, rectY;      // Position of square button
int rectSize = 60;     // Diameter of rect
color rectColor;
color red = color(200,0,0);
color green = color(0,200,0);
boolean rectOver = false;
boolean clicked = false;

Table table;

int numberOfData;

void setup() {
  size(1280, 800, P3D);
  
  table = loadTable("debug.csv");

  numberOfData = table.getRowCount();
  println(numberOfData);

  kalmanX = new float[numberOfData];
  kalmanY = new float[numberOfData];
  rpm = new float[numberOfData];
  for (int i = 0; i < numberOfData; i++) { // center all variables
    kalmanX[i] = height/2;
    kalmanY[i] = height/2;
    rpm[i] = height/2;
  }

  ellipseMode(CENTER);
  
  drawGraph(); // Draw graph at startup
}
int currentValue = 0;
boolean run = true;
void draw() { 
  
  if(run) {
   readTable();
   run=false;
  }
  else {
    drawGraph();
  }
  
  fill(150,150,150);
  textSize(20);
  text("currentCount", 10, 30); 
  text(currentValue, 140, 30); 
  text("angleX", 10, 60); 
  text(table.getInt(currentValue+1, 2), 140, 60); 
  text("angleY", 10, 90); 
  text(table.getInt(currentValue+1, 3), 140, 90); 
  text("RPM", 10, 120); 
  text(table.getInt(currentValue+1, 1), 140, 120); 

  stroke(80, 80, 80);// Red
  line(currentValue*(width/(kalmanX.length-2)),height/2,currentValue*(width/(kalmanX.length-2)),height);
  stroke(0,0,0);
  


  
  translate(width/2, height/4, 0);
  //if(currentValue != 0) {
    rotateX(table.getInt(currentValue+1, 2));
    rotateZ(table.getInt(currentValue+1, 3));
 // }
 
  //directionalLight(204, 204, 204, width/2, height/2, 20);
  fill(100,100,100);
  stroke(0); 
  box(150, 150, 150);
  beginShape(QUADS);
  vertex(-75, -75, -75);
  vertex( 75, -75, -75);
  vertex( 75, -75,  75);
  vertex(-75, -75,  75);
  endShape(); 
  delay(100);
}

void drawGraph() {
  background(255); // White
  for (int i = 0; i < width; i++) {
    stroke(200); // Grey
    line(i*10, height/2, i*10, height);
    line(0, height/2+i*10, width, height/2+i*10);
  }

  stroke(0); // Black
  for (int i = 2; i <= 3; i++)
    line(0, height/4*i, width, height/4*i); // Draw line, indicating -90 deg, 0 deg and 90 deg
  
  if(run) {
    convert();
    //translate(width/2, height/1.5, 0);
    drawAxisX(true);
    drawAxisY(true);
    drawAxisRPM(true);
  }
  else {
    drawAxisX(false);
    drawAxisY(false);
    drawAxisRPM(false);
  }
  
}

void readTable() {
  for (TableRow row : table.rows()) {
      angleX = row.getFloat(2);
      stringKalmanX = row.getString(2);
      angleY = row.getFloat(3);
      stringKalmanY = row.getString(3);
      stringRPM = row.getString(1);
      drawGraph();
  }
  
  //drawValues = true; // Draw the graph

  //printAxis(); // Used for debugging
}

void printAxis() {
  print(stringKalmanX);

  print('\t');

  print(stringKalmanY);

  println();
}

void keyPressed() {
  if (key == CODED) {
    if (keyCode == LEFT) {
      if(currentValue != 0) {
        currentValue--;
      }
    } else if (keyCode == RIGHT) {
      if(currentValue != numberOfData-2) {
        currentValue++;
      }
    } 
  } 
}

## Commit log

2017-02-08 finally uploaded something; first commit
    [bumper.scad, bumperForm.scad, completeModel.scad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]
2017-02-08 changed imu examples and added first version of a framework
2017-02-08 changed some imu files
2017-02-08 added Framework including the functions for all hardware modules
    [bumper.scad, bumperForm.scad, completeModel.scad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]
2017-02-08 removed Framework
2017-02-08 added Framework including functions for the hardware
2017-02-08 added first version of a landing secuence and added continious intervall timer controlled servo control to the framework
2017-02-11 continued on Framework
2017-02-11 added various debug messeges to the framework
2017-02-12 changes the initial speed of the motors and increased the servo slew distances
2017-02-13 changed Framework parameters and edited the ble com file
2017-02-15 added imu-value-visualizer(not working yet), changed the HWSERIAL Routine (two HM-11 BLE modules pared)
    [debug.csv]
2017-02-16 finished debug visualisation software and paired the two hm11 ble modules
    [debug.csv]
2017-02-16 finished the debugGraph Software, added temporary debug functionality to the framework
    [debug2243verySuccessful.csv, debug2243verySuccessfulCorrected.csv, hexagon.dxf]
2017-02-17 added firmware for the presentation of the different functions - not working yet
    [RoflCopterPresentationMode.ino]
2017-02-23 fixed esc test firmware; was mixed up with servo test firmware
    [RoflCopterPresentationMode.ino, klappenTest.ino]
2017-05-12 more detailes debug logs and reduced baud rate to reduce debug log transmission errors
    [flightControler.ino]
2017-05-13 static motor control and more logging foo
2017-05-14 added landing sequence
2017-05-14 checked landing foo
2017-05-16 fixed rx ppm fail (sync break wasn't always >8ms)
    [RoflCopterFramework.ino, flightControler.ino]
2017-05-16 fixed the motor start serial error
    [flightControler.ino]
2017-05-16 reviewed the angle functions; encountered some problems which will be fixed tomorrow
    [flightControler.ino]
2017-05-16 fixed angle calculation problem by converting the rad value to degree...
    [flightControler.ino]
2017-05-17 fixed the results of my mathematical stupidness
    [flightControler.ino]
2017-05-22 changed the speed parameter for the motor control
2017-05-22 finetuned the motor speed
2017-05-22 tested the hardware timer to control the flaps
2017-10-24 add latest scad file
    [completeModelnew5.scad]
2017-10-24 add screwprop scad file which is a dependency of the latest scad file of the model
    [screwprop.scad]
2017-10-24 add screwprop file which is a dependency of the model files
    [screwprop.scad]
2017-10-24 update design of model (switched Teensy 3.2 to DIPFORTy1 by TrezElectronic) and add NACA0009 to rotor design project
    [completeModel0.scad]
2017-10-25 just some design experiments
    [completeModel0.scad]
2017-10-25 add naca profiles
    [bladeNACA0012.scad, completeModel0.scad]
2017-10-25 rotorblade vortex analysis
    [rotorbladeOnly(extracted from completeModel0).scad, rotorbladesOnly.stl]
